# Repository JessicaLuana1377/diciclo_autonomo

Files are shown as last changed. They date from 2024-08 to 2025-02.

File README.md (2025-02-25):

# Diciclo Autonomo

Este repositório reúne todos os recursos necessários para o desenvolvimento de um diciclo autônomo, também conhecido como pêndulo invertido sobre rodas. Nele, você encontrará códigos para modelagem, controle e experimentação, bem como técnicas para a identificação de parâmetros complexos que são cruciais para o comportamento dinâmico do sistema. Além disso, o repositório oferece materiais que abrangem tanto a parte teórica, para o entendimento do funcionamento, quanto a parte prática, voltada para a construção e implementação do projeto.



## Tabela de conteúdos
- [Motivação](#motivação)
- [Primeiros passos](#primeiros-passos)
- [Modelagem](#modelagem)
- [Controle](#controle)
- [Credits](#credits)

## Motivação
- Falta de projetos que unam a parte teórica de modelagem e controle com a prática de implementação.

- Oferecer um projeto simples de replicar e entender, tornando mais fácil o acesso às técnicas de controle e automação.

- Desenvolver um projeto acessível financeiramente, já que muitos dispositivos e projetos prontos são caros e difíceis de adquirir.

## Primeiros passos

#### Lista de componentes
* 1 ESP32;
* 2 Motores DC - Mini motor DC com caixa de redução, 6 V e 500 RPM;
* 1 Regulador de tensão - Ponte H L298N;
* 1 IMU - MPU6050;
* 1 Suporte de pilhas;
* 2 Pilhas - Pilha de lítio de 3,7 V cada;
* 1 Botão chave On/Off;
* Base do díciclo autônomo - Arquivo .stl para impressão 3D;
* 1 Cabo para soldar e 12 cabos com conectores fêmea dos 2 lados;
* 10 Parafusos M2;
* 2 Parafusos M2 com cabeça achatada;
* 2 Parafusos M2 longos para proteção;
* 2 Parafusos M1.5 para os motores.

#### Montagem

Inicialmente, monte os componentes na estrutura conforme as figuras abaixo:

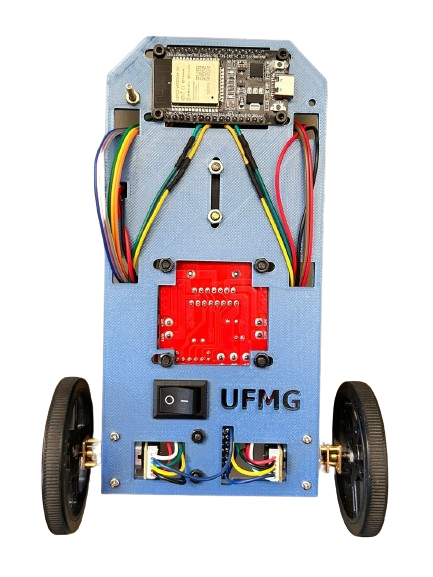
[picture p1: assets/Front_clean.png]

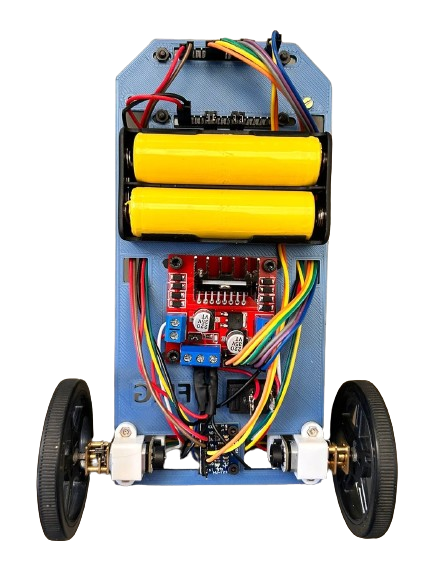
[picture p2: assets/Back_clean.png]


Em seguida, solde um dos terminais da chave On/Off com o cabo e o outro terminal com a alimentação do suporte de pilha (cabo vermelho).
E por fim, complete o circuito seguindo o diagrama elétrico  representado na figura abaixo:

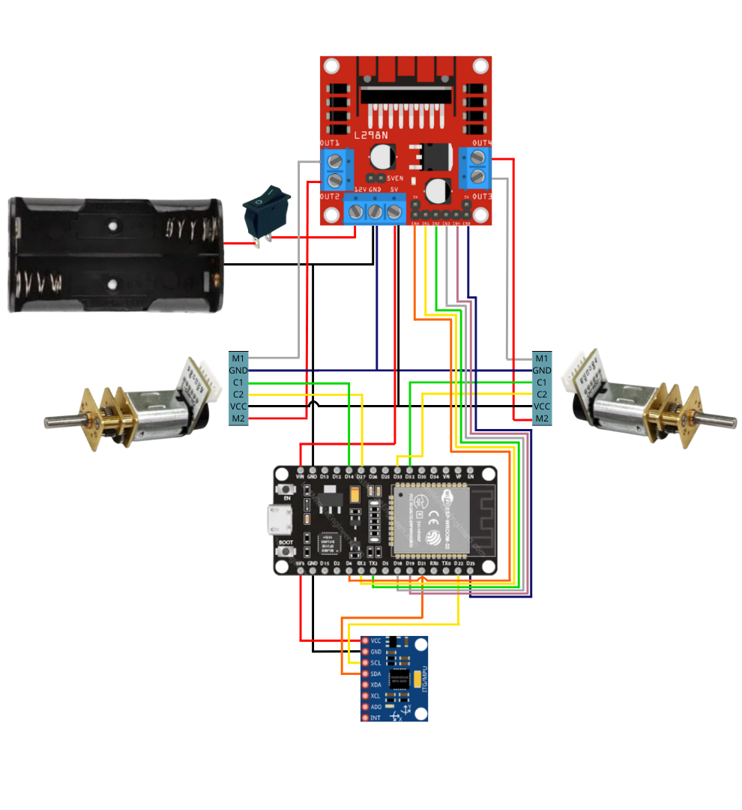
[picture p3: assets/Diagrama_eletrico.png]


#### Software 

1. Acesse o site oficial do Arduino, ou clique [aqui](https://www.arduino.cc/en/software), e baixe a versão do Arduino IDE correspondente ao seu sistema 
2. Instale o driver do ESP32 depois de descompactar o arquivo "CP210x_Windows_Drivers.zip" disponível na pasta [Programas auxiliares](https://github.com/JessicaLuana1377/diciclo_autonomo/tree/main/Progamas%20auxiliares) do repositório, ou pesquise por "CP210x USB to UART Bridge", acesse o site oficial da Silicon Labs, vá na aba de downloads e baixe o arquivo "CP210x Universal Windows Driver". 
3. Instale a placa do ESP32 no Arduino IDE. Abra o Arduino IDE, vá em Tools > Board > Board Manager, pesquise por esp32 by Espressif Systems, selecione a versão 2.0.17 e instale.
4. Instale as bibliotecas usadas no projeto. Vá em Sketch > Include Library > Manage Libraries pesquise e instale as bibliotecas: ESP32Encoder by Kevin Harriongton versão 0.11.6 e Adafruit MPU6040 by Adafruit versão 2.2.6 (Baixe todas as dependências dessa biblioteca).

Qualquer dúvida, o procedimento está mais detalhado na seção 2.4 do [Manual de desenvoltimento](https://github.com/JessicaLuana1377/diciclo_autonomo/blob/main/Manual%20de%20desenvolvimento.pdf).

Realizando todos os passos corretamente, é possivel carregar qualquer um dos códigos disponíveis no ESP32.

#### Testes
  A pasta [CodigosDisponiveis](https://github.com/JessicaLuana1377/diciclo_autonomo/tree/main/CodigosDisponiveis) tem 3 arquivos:
  - IMU: Contém um código de teste para o funcionamento da IMU;
  - Encoder: Contém um código de teste para o funcionamento e serve para garantir que os pinos estão corretamente conectados;
  - Controle de velocidade: Contém 3 arquivos, sendo eles
      - Um arquivo .mlx que aborda detalhadamente a modelagem e o controle de um motor, utilizando dados reais para determinar o modelo de um motor específico, além de outros dados experimentais que comprovam a eficácia do controlador;
      - Um código para obter os dados de um motor para modelagem;
      - Um código de controle que também exporta os dados para monitorar e analisar o desempenho do controlador;
      - Um arquivo .txt com dados experimentais de exemplo para modelagem;
      - Um arquivo .txt com dados experimentais de exemplo do controle.

## Modelagem
A modelagem do sistema está disponível no arquivo "Modelo_novo.mlx", na pasta [Modelo](https://github.com/JessicaLuana1377/diciclo_autonomo/tree/main/Modelo). Para obter o modelo corretamente, deve-se alterar os valores das variáveis no tópico "Valores das variáveis" dentro do arquivo e executar os experimentos do [Corpo](https://github.com/JessicaLuana1377/diciclo_autonomo/tree/main/Modelo/Corpo) e das [Rodas](https://github.com/JessicaLuana1377/diciclo_autonomo/tree/main/Modelo/Rodas), antes de executar o arquivo "Modelo_novo.mlx". Após realizar os experimentos, execute o arquivo "Modelo_novo.mlx" e ele irá gerar o modelo do seu pêndulo e exportar os dados necessários para a pasta de [Controle](https://github.com/JessicaLuana1377/diciclo_autonomo/tree/main/Controle). Evite trocar os arquivos de diretórios para que funcionem corretamente.

## Controle
Na pasta [Controle](https://github.com/JessicaLuana1377/diciclo_autonomo/tree/main/Controle) está disponível o desenvolvimento de um controlador Compensador de Avanço e Atraso no arquivo "Compensador.mlx". O arquivo "fts.mat" deve ter sido gerado a partir do seu modelo, portanto, tenha certeza que o arquivo de modelagem foi completamente executado antes de vir para este passo. Após realizar os ajustes necessários no controlador, pegue os ganhos disponíveis no tópico "Ganhos discretizados dos controladores" e substitua no arquivo "controle_lead_lag.ino" disponível na pasta [controle_lead_lag](https://github.com/JessicaLuana1377/diciclo_autonomo/tree/main/Controle/controle_lead_lag). Teste seu controlador e realize ajustes finos caso seja necessário.
Outro controlador esta disponível na pasta [Controle](https://github.com/JessicaLuana1377/diciclo_autonomo/tree/main/Controle), é um controlador avançado LQR com integrador e uma implementação simples de um filtro de Kalman, caso tenha curiosidade, teste no seu pêndulo.

## Credits

## Authors

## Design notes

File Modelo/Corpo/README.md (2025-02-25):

## Experimento das Corpo

#### Experimento
Para realizar o experimento do corpo, no código da pasta [ExperimentoArduinoIDE](https://github.com/JessicaLuana1377/diciclo_autonomo/tree/main/Modelo/ExperimentoArduinoIDE) descomente as linhas referentes ao f0, f1 e MAX_PWM do experimento do corpo e carregue o código no ESP32. Clique no botão ‘En’ do ESP32 e, quando uma luz azul piscar, clique no outro botão (‘Boot’). O experimento deve ser realizado segurando as rodas do diciclo e deixando-o pendurado, livre para que o corpo possa balançar. Mantenha-o estável durante todo o experimento e sem o cabo para não prejudicar a captura de dados. Se, em algum momento, o corpo do diciclo bater em algum lugar, diminua a variável MAX\_PWM e recomece o experimento. Espere o experimento terminar. Com o ESP32 conectado no computador, abra a ferramenta ‘CoolTerm.exe’ disponível na internet e na pasta [Programas auxiliares](https://github.com/JessicaLuana1377/diciclo_autonomo/tree/main/Progamas%20auxiliares) (não é necessário instalar o programa, apenas descompactar o arquivo e executar a ferramenta). 

#### Configuração do CoolTerm
Em ‘Options’, no campo ‘Baudrate’, selecione a velocidade da serial configurada no ESP32; caso não tenha alterado, é 115200. Para salvar os dados em um arquivo, vá em ‘Connection’, ‘Capture to text/binary file’, ‘Start’, escolha o diretório do arquivo sendo a pasta ‘Rodas’ e coloque o nome ‘exp_rodas_bruto’. Para conectar a ferramenta com o ESP32, confira se o Serial Monitor de todas as abas do Arduino IDE está fechado, clique em ‘Connect’ e espere o ESP32 parar de piscar a luz azul.

#### Leitura dos dados
Ao clicar em ‘l’, serão listados todos os arquivos presentes na flash do ESP32. A cada nova simulação, é criado um novo arquivo, começando com o nome ‘Arquivo0’, ‘Arquivo1’, etc. A letra ‘f’ apaga todos os arquivos. A letra ‘r’ lê e, em seguida, apaga todos os arquivos e ‘R’ apenas lê, mantendo todos na memória.
Realize a leitura com ‘r’ ou ‘R’ e, quando terminar a leitura, pare a gravação do arquivo em ‘Connection’, ‘Capture to text/binary file’, ‘Stop’. Vá no arquivo ‘exp_rodas_bruto.txt’ e apague as linhas desnecessárias, deixando apenas o cabeçalho e os dados (vá ao final do arquivo e apague todas as linhas em branco).

#### Tratamento e escolha de dados
No arquivo ‘TratarDados.mlx’ descomente as linhas referentes ao experimento do corpo presentes no início e no final do arquivo e o execute. Nele estão dispostos gráficos para verificação dos dados, alguns pontos devem ser conferidos:
    • A frequência inicial deve ser pequena o suficiente para que o início do gráfico de velocidade apresente um ganho constante;
    • A frequência final não deve ser muito alta para não capturar muito ruído;
    • O tempo da chirp deve ser grande o suficiente para dar tempo do motor reagir à entrada;
    • Repita os experimentos com novos valores para as variáveis, se necessário.
Ao final do arquivo "TratarDados.mlx" é gerado um arquivo de dados com extensão do MATLAB que será usado em "ExperimentoCorpo.mlx". Execute-o e serão apresentados 6 modelos: dois baseados na posição fornecida pelo encoder de cada roda, dois baseados na velocidade de cada roda, 1 baseado na posição da MPU e 1 baseado na velocidade da MPU. Escolha o que melhor corresponde ao experimento e substitua no final. Execute o arquivo novamente e serão salvos os dados do modelo correto para serem usados no modelo do pêndulo.

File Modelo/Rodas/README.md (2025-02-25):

## Experimento das Rodas

#### Experimento
Para realizar o experimento das rodas, coloque o código da pasta [ExperimentoArduinoIDE](https://github.com/JessicaLuana1377/diciclo_autonomo/tree/main/Modelo/ExperimentoArduinoIDE) no ESP32 do diciclo, descomente as linhas referentes ao f0, f1 e MAX_PWM do experimento das rodas e coloque o diciclo em uma superfície estável, onde as rodas estejam livres. Clique no botão ‘En’ do ESP32 e, quando uma luz azul piscar, clique no outro botão (‘Boot’). Espere o experimento terminar. Com o ESP32 conectado no computador, abra a ferramenta ‘CoolTerm.exe’ disponível na internet e na pasta [Programas auxiliares](https://github.com/JessicaLuana1377/diciclo_autonomo/tree/main/Progamas%20auxiliares) (não é necessário instalar o programa, apenas descompactar o arquivo e executar a ferramenta). 

#### Configuração do CoolTerm
Em ‘Options’, no campo ‘Baudrate’, selecione a velocidade da serial configurada no ESP32; caso não tenha alterado, é 115200. Para salvar os dados em um arquivo, vá em ‘Connection’, ‘Capture to text/binary file’, ‘Start’, escolha o diretório do arquivo sendo a pasta ‘Rodas’ e coloque o nome ‘exp_rodas_bruto’. Para conectar a ferramenta com o ESP32, confira se o Serial Monitor de todas as abas do Arduino IDE está fechado, clique em ‘Connect’ e espere o ESP32 parar de piscar a luz azul.

#### Leitura dos dados
Ao clicar em ‘l’, serão listados todos os arquivos presentes na flash do ESP32. A cada nova simulação, é criado um novo arquivo, começando com o nome ‘Arquivo0’, ‘Arquivo1’, etc. A letra ‘f’ apaga todos os arquivos. A letra ‘r’ lê e, em seguida, apaga todos os arquivos e ‘R’ apenas lê, mantendo todos na memória.
Realize a leitura com ‘r’ ou ‘R’ e, quando terminar a leitura, pare a gravação do arquivo em ‘Connection’, ‘Capture to text/binary file’, ‘Stop’. Vá no arquivo ‘exp_rodas_bruto.txt’ e apague as linhas desnecessárias, deixando apenas o cabeçalho e os dados (vá ao final do arquivo e apague todas as linhas em branco).

#### Tratamento e escolha de dados
No arquivo ‘TratarDados.mlx’ descomente as linhas referentes ao experimento das rodas presentes no início e no final do arquivo e o execute. Nele estão dispostos gráficos para verificação dos dados, alguns pontos devem ser conferidos:
    • A frequência inicial deve ser pequena o suficiente para que o início do gráfico de velocidade apresente um ganho constante;
    • A frequência final não deve ser muito alta para não capturar muito ruído;
    • O tempo da chirp deve ser grande o suficiente para dar tempo do motor reagir à entrada;
    • Repita os experimentos com novos valores para as variáveis, se necessário.
Ao final do arquivo "TratarDados.mlx" é gerado um arquivo de dados com extensão do MATLAB que será usado em "ExperimentoRodas.mlx". Execute-o e serão apresentados 4 modelos: dois baseados na posição fornecida pelo encoder de cada roda e dois baseados na velocidade de cada roda. Escolha o que melhor corresponde ao experimento e substitua no final. Execute o arquivo novamente e serão salvos os dados do modelo correto para serem usados no modelo do pêndulo.

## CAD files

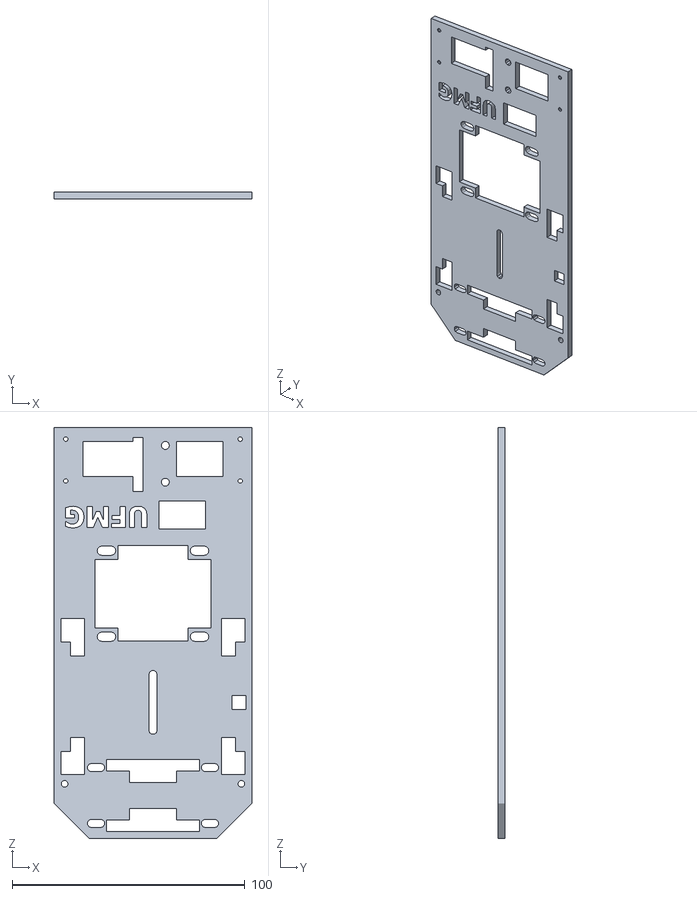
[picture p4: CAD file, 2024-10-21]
Estrutura/Base_Final_UFMG_V5.stl
85.0 x 3.00 x 176.7

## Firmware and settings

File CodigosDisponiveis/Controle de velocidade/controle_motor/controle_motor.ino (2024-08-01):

#include <ESP32Encoder.h>
#include <math.h>
#include <stdio.h>

#define ENCODER_C1_R 32
#define ENCODER_C2_R 33 
#define ENCODER_C1_L 14
#define ENCODER_C2_L 27

#define IN1 16
#define IN2 17
#define ENA 4

#define IN3 18
#define IN4 19
#define ENB 23

#define L_CHANNEL 0
#define R_CHANNEL 1

// Funções auxiliares
void motor(int PWM, int chanel);
void PinSetup();

// Variáveis Globais
const float TS = 10/1e3; // 10 milisegundos
const float Ti = 1/25.0; 
const float Kp = 3.75;

float t0, t;
unsigned long last_time;
ESP32Encoder encoder_r;
ESP32Encoder encoder_l;

float theta_ml, theta_mr; // posição angular do motor esquerdo e direito 
float last_theta_ml, last_theta_mr; 
float omega_ml, omega_mr; // velocidade angular do motor esquerdo e direito 
float u_ml, u_mr; // entrada dos motores
float error_ml, error_mr;
float sum_error_ml = 0, sum_error_mr = 0;

float ref = 0; // rad/s;

void setup() {
  Serial.begin(115200);
  PinSetup();

  motor(0, L_CHANNEL);
  motor(0, R_CHANNEL);

  printf("t;ref;u_ml;omega_ml;u_mr;omega_mr\n");

  delay(100);

  t0 = micros()/1e6;
}

unsigned long diff;
void loop() {
  if ((diff = micros() - last_time) >= TS*1e6) {
    last_time = micros();
    t = micros()/1e6 - t0; // tempo de simulação em segundos

    theta_ml = 2*PI * encoder_l.getCount()/(float)(4*7*30);
    theta_mr = 2*PI * encoder_r.getCount()/(float)(4*7*30);

    // calculo da velocidade: variação da posição sobre a variação do tempo -> (dtheta/dt)
    omega_ml = (theta_ml - last_theta_ml)/TS;
    omega_mr = (theta_mr - last_theta_mr)/TS;

    error_ml = ref - omega_ml;
    error_mr = ref - omega_mr;
    // integral do erro: somatório das áreas dos trapézios -> sum(erro * dt)
    sum_error_ml += error_ml * TS; 
    sum_error_mr += error_mr * TS; 

    u_ml = Kp * (error_ml + sum_error_ml/Ti);
    u_mr = Kp * (error_mr + sum_error_mr/Ti);

    motor(u_ml, L_CHANNEL);
    motor(u_mr, R_CHANNEL);

    // Descomente para observar as saídas no Arduino Serial Plot
    printf("limInf:-30,limSup:30,ref:%.04f,omega_ml:%.04f,omega_mr:%.04f\n", 
      ref, omega_ml, omega_mr);

    // Ou descomente este para ler os dados no CoolTerm
    // printf("%.04f;%.04f;%.04f;%.04f;%.04f;%.04f\n", t, ref, u_ml, omega_ml, u_mr, omega_mr);

    last_theta_ml = theta_ml;
    last_theta_mr = theta_mr;
  }

  if (t >= 3 && t < 6) { // referência 1
    ref = 2*PI;
  } else if (t >= 6 && t < 9) { // referência 2 
    ref = 4*PI;
  } else if (t >= 9 && t < 12) { // referência 3
    ref = 8*PI;
  } else if (t >= 12 && t < 15) { // referência 4
    ref = -8*PI;
  } else { // referência final
    ref = 0;
  }
}

void PinSetup() {
  // Configuração dos pinos
  pinMode(IN1, OUTPUT);
  pinMode(IN2, OUTPUT);
  pinMode(IN3, OUTPUT);
  pinMode(IN4, OUTPUT);

  // Configuração do PWM
  ledcSetup(L_CHANNEL, 200, 8);
  ledcSetup(R_CHANNEL, 200, 8);
  ledcAttachPin(ENA, L_CHANNEL);
  ledcAttachPin(ENB, R_CHANNEL);
  ledcWrite(L_CHANNEL, 0);
  ledcWrite(R_CHANNEL, 0);

  // Configuração dos encoders
  ESP32Encoder::useInternalWeakPullResistors = puType::up;
	encoder_r.attachFullQuad(ENCODER_C1_R, ENCODER_C2_R);
	encoder_l.attachFullQuad(ENCODER_C1_L, ENCODER_C2_L);
  encoder_r.clearCount();
  encoder_l.clearCount();
}

void motor(int PWM, int chanel) {
  int p1, p2;
  if (chanel == L_CHANNEL) {
    p1 = IN1;
    p2 = IN2;
  } else {
    p1 = IN3;
    p2 = IN4;
  }
  PWM = constrain(PWM, -100, 100); // saturador
  PWM = map(PWM, -100, 100, -255, 255); // altera a escala de -100:100 para -255:255
  if (PWM > 0) {
    digitalWrite(p1, LOW);
    digitalWrite(p2, HIGH);
  } else if (PWM < 0) {
    PWM = -PWM;
    digitalWrite(p1, HIGH);
    digitalWrite(p2, LOW);
  } else {
    digitalWrite(p1, LOW);
    digitalWrite(p2, LOW);
  }
  ledcWrite(chanel, PWM);
}

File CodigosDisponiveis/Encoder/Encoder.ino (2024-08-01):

#include <ESP32Encoder.h>
// Pinos do encoderes
#define ENCODER_C1_R 32
#define ENCODER_C2_R 33 
#define ENCODER_C1_L 14
#define ENCODER_C2_L 27
#define TS 500 // Tempo de amostragem em milissegundos

// Pinos dos motores
#define IN1 16
#define IN2 17
#define ENA 4

#define IN3 18
#define IN4 19
#define ENB 23

// Canais de PWM
#define L_CHANNEL 0
#define R_CHANNEL 1

// Variaveis dos encoder
ESP32Encoder encoder_r;
ESP32Encoder encoder_l;

unsigned long t0 = millis();
void setup() {
  Serial.begin(115200);
  delay(100);

  // Configuração dos pinos
  pinMode(IN1, OUTPUT);
  pinMode(IN2, OUTPUT);
  pinMode(IN3, OUTPUT);
  pinMode(IN4, OUTPUT);

  // Configuração do PWM
  ledcSetup(L_CHANNEL, 200, 8);
  ledcSetup(R_CHANNEL, 200, 8);
  ledcAttachPin(ENA, L_CHANNEL);
  ledcAttachPin(ENB, R_CHANNEL);
  ledcWrite(L_CHANNEL, 0);
  ledcWrite(R_CHANNEL, 0);

  // Configuração dos encoders
  ESP32Encoder::useInternalWeakPullResistors = puType::up;
	encoder_r.attachFullQuad(ENCODER_C1_R, ENCODER_C2_R);
	encoder_l.attachFullQuad(ENCODER_C1_L, ENCODER_C2_L);
  encoder_r.clearCount();
  encoder_l.clearCount();
}

void loop() {
  if (millis() - t0 > TS){
    t0 = millis();
    float position_r = encoder_r.getCount();
    float position_l = encoder_l.getCount();

    // Comente essas duas linhas para testar o encoder individualmente
    motor(10,L_CHANNEL);
    motor(100,R_CHANNEL);

    Serial.print(" Encocer direito: ");
    Serial.print(position_r);
    Serial.print(" Encocer esquerdo: ");
    Serial.print(position_l);
    Serial.println();
  }
}

void motor(int PWM, int chanel) 
{
  int p1, p2;
  if (chanel == L_CHANNEL) 
  {
    p1 = IN1;
    p2 = IN2;
  } else {
    p1 = IN3;
    p2 = IN4;
  }
  PWM = constrain(PWM, -100, 100);
  PWM = map(PWM, -100, 100, -255, 255);
  if (PWM == 0) 
  {
    digitalWrite(p1, LOW);
    digitalWrite(p2, LOW);
    return;
  } else if (PWM > 0) 
  {
    digitalWrite(p1, LOW);
    digitalWrite(p2, HIGH);
  } else 
  {
    PWM = -PWM;
    digitalWrite(p1, HIGH);
    digitalWrite(p2, LOW);
  }
  ledcWrite(chanel, PWM);
}

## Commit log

2024-07-02 arduino-experimento limpo e funcionando
2024-07-13 Códigos de testes adicionados
2024-08-04 Tempo de amostragem e modelagem das rodas corrigidos
    [ExperimentoArduinoIDE.ino, tools.cpp, tools.h]
2024-08-12 Experimentos corrigidos e organizados
    [ExperimentoArduinoIDE.ino, tools.cpp]
2024-08-12 Controlador funcionando, conferir tempos de amostragem no matlab
2024-10-21 Adicionada a estrutura em stl
    [Base_Final_UFMG_V5.stl]
2025-02-18 Atualizações no ReadMe e adição de imagens e Manual
